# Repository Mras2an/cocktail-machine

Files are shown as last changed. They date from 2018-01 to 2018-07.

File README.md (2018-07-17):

# cocktail-machine

The goal is to be able to:
- Order a cocktail via a phone or PC
- Order a cocktail via a voice assistant (Google home, Alexa, ...).
- Order a cocktail via a IFTTT trigger

You have full documentation into the doc repertory.

## DEMO :

<a href="https://www.youtube.com/watch?v=Tx3ExhTUp6A" target="_blank">WebcamIP</a>

## CALL FOR VOLUNTEERS

After this first version I'm looking for people to help me on this open source project. The goal is to propose "pull requests" for new features or modifications.

Here is the list of features to improve the project (Do not hesitate to propose others):

| State | Addons
|---|---
| todo | Submit an UX (User eXperience) and a design for the web page
|  todo | Re-make the web page (css / html) according to the UX / design
| todo | Handling several languages on the web page
| todo | Fix the smartconfig bug
| todo | Fix potential bug
| todo | Add auto tests
| todo | Delete wifi ssid / mdp with push button
| todo | Re-make the socket part for IFTTT
| todo | Reset the A4988 module when the step motors are not used
| todo | Use the PWM for LED handling
| todo | Create doxygen documentation
| todo | And more ...

I know that any job deserves a salary but I have nothing to you offer. But I can send you a bare PCB  to make your own machine (only for the first 5 most motivated volunteers).

Please, if you are interested here is the mailing list to discuss new features or modifications: "connectedcocktailmachine@gmail.com"

Thank you for your time.

## LICENSE TERMS 

Copyright (c) 2018. Redistribution and use in source and binary forms, with or without
modification, are permitted provided that the following conditions are met:

* please cite the project [Mras2an] http://mras2an.webnode.fr/

THIS SOFTWARE IS PROVIDED BY THE REGENTS AND CONTRIBUTORS 'AS IS' AND ANY
EXPRESS OR IMPLIED WARRANTIES, INCLUDING, GO TO NOT LIMITED TO, THE IMPLIED
WARRANTIES OF MERCHANTABILITY AND FITNESS FOR A PARTICULAR PURPOSE ARE
DISCLAIMED.

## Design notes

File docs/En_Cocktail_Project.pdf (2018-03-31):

## Realization of a connected cocktail machine with an espressif WROOM32

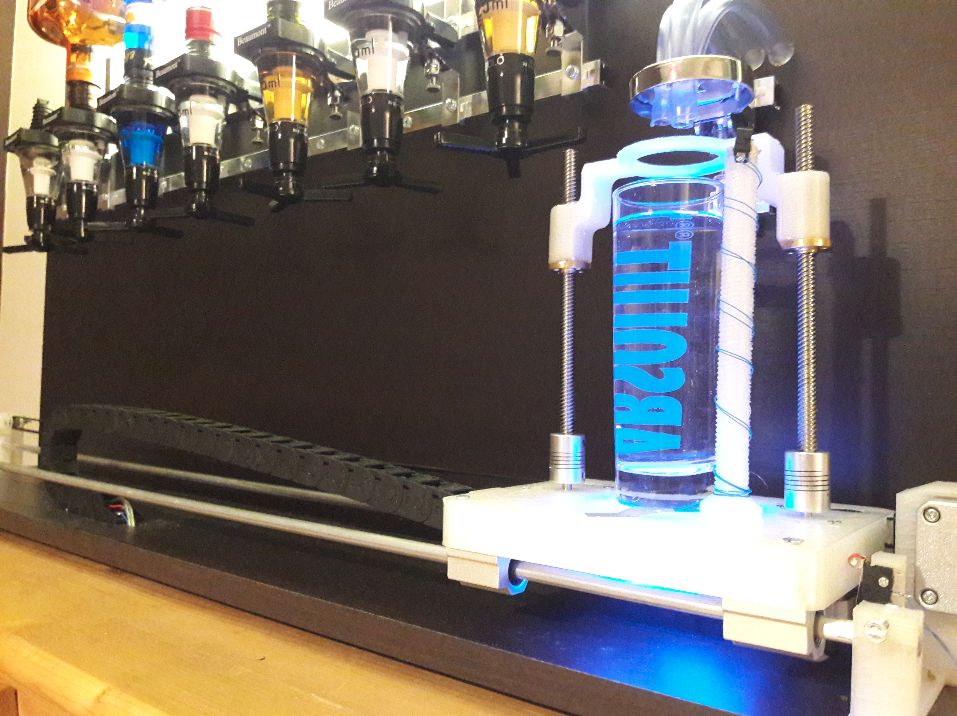
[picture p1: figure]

Revision | Data | Author | Modifications
R01 | 17/01/2018 | Q.THEROND | Creation

1) Introduction | 3
2) Sagittal diagramme | 4
2.1) Description of the links | 4
3) Functional diagram | 5
3.1) FS1.0: Power supply | 5
3.2) FS1.1: Stepper motors | 5
3.3) FS1.2: RGB LED | 6
3.4) FS1.3: uC wifi | 6
3.5) FS1.4: Sensors | 6
3.6) FS1.5: Pumps | 6
3.7) FS1.6: Expansion connectors | 7
4) Structural diagram | 8
4.1) FS1.0: Power | 9
4.1.1) Calculation of a radiator | 10
4.2) FS1.1: Step motors | 11
4.3) FS1.2: RGB LED | 12
4.4) FS1.3 : uC wifi | 13
4.4.1) Definition of the inputs, outputs of the microcontroller. | 13
4.4.1.1) Inputs | 13
4.4.1.2) Outputs | 14
4.4.1.3) Other: | 14
4.5) FS1.4: Sensors | 15
4.6) FS1.5: Pumps | 16
4.7) FS1.6: Expansion connectors | 17
5) The PCB and List of components | 18
5.1) PCB | 18
5.2) PCB List of components | 19
5.3) Meca and other: | 20
6) The software | 22
6.0) Presentation of Wifi/Bluetooth WROOM-32 module and SDK-IDF | 22
6.0.1) WROOM-32 module | 22
6.0.2) SDK-IDF | 22
6.1) Flash partition | 22
6.2) The architecture | 24
6.2.1) The espressif SDK | 24
6.2.2) The drivers | 24
6.2.3) The HAL and OSAL | 24
6.2.4) The application | 24
6.3) The features of the software | 25

6.3.1) Wi-Fi connected mode | 25
6.3.2) smartconfig mode | 26
6.3.3) Update (OTA) | 27
6.3.4) Push button | 27
6.3.5) File system | 28
6.3.6) End-of-run detection | 29
6.3.7) Web page for the cmd cocktails | 29
6.3.8) Motor control | 31
6.3.9) Step motor control | 31
6.3.10) RGB LED | 32
6.3.11) cJson | 32
6.3.12) mDNS hostname | 33
6.3.13) Voice assistant (Alexa, Google Home, ...) | 33
6.3.13.1) Configure NAT and dynDNS | 33
6.3.13.2) Create an Applet on IFTTT | 33
6.3.13.3) Open a TCP socket on the ESP32 | 34
6.3.14) Logs | 35
6.3.15) Add-on | 35
6.4) The JSON | 36
6.4.1) The JSON of the location of the bottles | 36
6.4.2) The JSON of the cocktail ingredient list. | 36
6.5) The web page | 37
6.5.1) The CSS | 37
6.5.1) HTML | 38
7) Mechanics | 40
7.1) The wood | 40
7.2) The tray | 40
8) Getting started and functioning | 41
8.1) Hardware connection | 41
8.2) Configure the software | 41
8.3) Compile and program the code | 42
8.4) First boot | 42
8.4) Movies | 44
8.5) Hygiene of the cocktail machine | 44
9) The future of the project | 45
9.1) Modify | 45
9.2) Add | 45
10) Pictures | 46

# 1) Introduction

Failing to achieve an interesting feature for the espressif SDK like wi-fi mesh I will present a fun project. The realization hardware and software of a connected cocktail machine with an espressif WROOM32. The goal is to be able to:
- Order a cocktail via a phone or PC
- Order a cocktail via a voice assistant (Google home, Alexa, ...).
- Order a cocktail via a IFTTT trigger

For that we will see different IOT functionality proposed by the WROOM32 like:
- Connect the system to internet with smartconfig
- Create a web page
- Use a mDNS and a fixed IP.
- Use a socket for IFTTT
- Update the system with OTA and the flash partition of ESP32
- Use the hardware features on the ESP (gpio, file system, ...)
- Use the FreeRTOS operating system of the espressif SDK-IDF
- Use the cJson library

And sorry for my English!

# 2) Sagittal diagramme

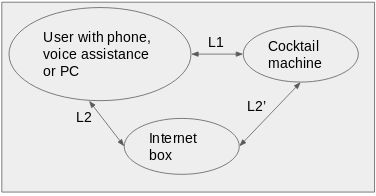
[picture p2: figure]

## 2.1) Description of the links

L2 / L2 ':
- Allows the user to order a cocktail via a web page.
- Allows the user to order a cocktail via a voice assistance (Alexa, Google Home, ...)
- Send his SSID and password with his smartphone to connect the system to the internet.
- Allows the system update with OTA
L1:
- Allows the user to put and retrieve his glass.
- Lighting information about the state of the system.
- Allows fill the bottles and clean them.

# 3) Functional diagram

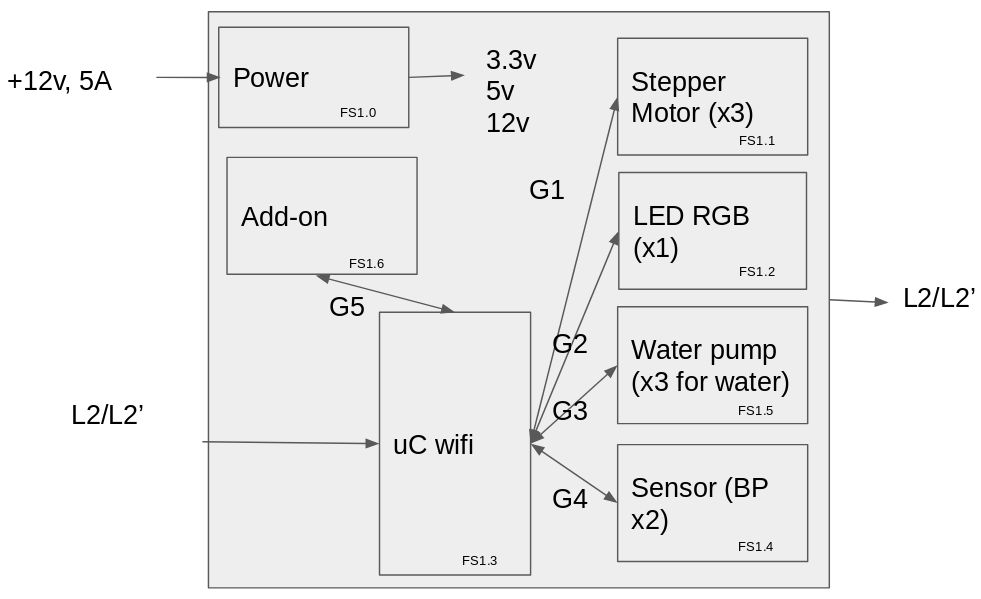
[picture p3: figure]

## 3.1) FS1.0: Power supply

The power function allows to create, thanks to an input voltage of 12V 5A, + 5V, + 3.3V, 0V.

Input(s):
12V, 5ADC.

Output(s):
+ 5V, + 3.3V, 0V

## 3.2) FS1.1: Stepper motors

The motor function allows to control the tray with the glass and to serve the cocktail via the dosers.

Input(s):
G1: Digital signals (dir and clk) for controlling the stepper motors.

Output(s):
Physical movement of the engines

## 3.3) FS1.2: RGB LED

The RGB LED informs the user of the system status.

Input(s):
G2: Digital signals to control the RGB LED.

Output(s):
L2: Lighting signals to inform the user

## 3.4) FS1.3: uC wifi

Ensures through a programmed treatment (software) the acquisition, processing and return of information. The smartconfig mode of the wroom32 allows to recover the SSID and password of the internet box. The wi-fi allows to control the system via a smartphone or a computer through a web page on a fixed IP address or with a voice assistance. It communicates with the motors, the RGB LED. sensors, and offers inputs / outputs to add additional functionality.

Input(s):
L2 / L2 ': Wifi connection in wpa2, wep, ... smartconfig mode, http web page, socket for IFTTT, OTA update
G4: Digital Signals for Limit Detection

Output(s):
L2 / L2 ': Wifi connection in wpa2, wep, ... smartconfig mode, http web page, socket for IFTTT, OTA update
G1: Digital Signals for Stepper Motor Control
G2: Digital Signals for RBG LED Control
G3: Digital signals for pump control

## 3.5) FS1.4: Sensors

Allows to delete the SSID and password of the wi-fi with a push button and the end-of-run detections.

Input(s):
L1: Physical size

Output(s):
G4: Digital signals on / off

## 3.6) FS1.5: Pumps

The "pumps" function is used to control DC motors.

Input(s):
G3: Digital signals for pump control

Output(s):
Physical movement.

## 3.7) FS1.6: Expansion connectors

Allows you to add features to the e-card.

Input(s):
G5: Digital Signals

Output(s):
G5: Digital Signals

# 4) Structural diagram

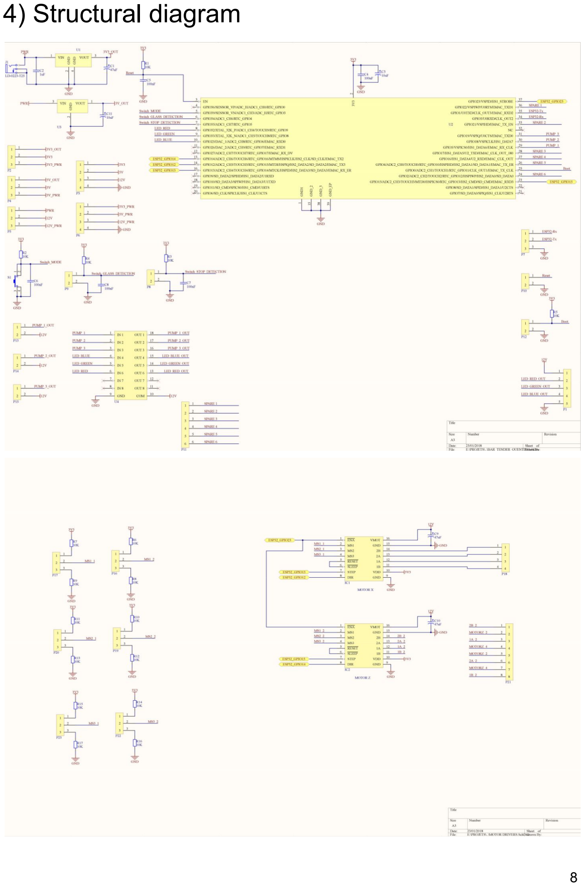
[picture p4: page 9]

## 4.1) FS1.0: Power

The power function allows to create, thanks to an input voltage of 12V 5A, + 5V and + 3.3V.

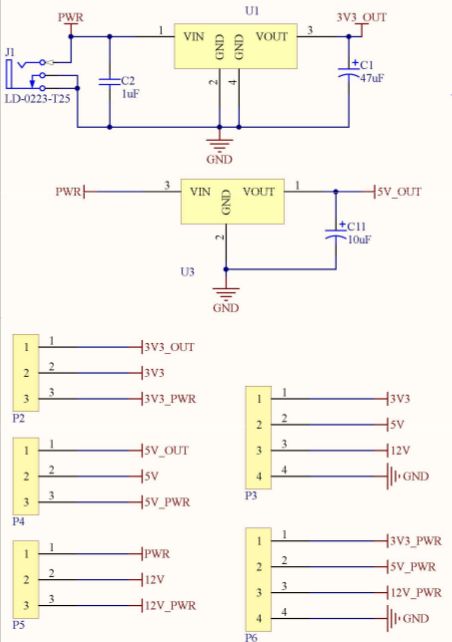
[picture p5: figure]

J1: 12v input

C1, C11: Polarized chemical capacitors. They perform the filtering, and allow a decoupling in case of power supply

C2: Plastic capacitor, serves as an anti-parasite to suppress high
frequencies (it is recommended in the technical documentation).

U3: 5V regulator, it allows to regulate the input voltage 12V DC in a voltage of 5V DC. According to the manufacturer's documentation of the 78XX, a minimum input voltage of the output voltage plus Vdrop (2V) or Ve = Vs + Vdrop = 5 + 2 = 7V minimum is required for proper operation.

U1: 3.3V LDO, it allows to regulate the input voltage 12V DC in a voltage of 3.3V DC.

P2, P4, P5: Choose the power source (internal or external) according to the current requirement. It is physically, connecting strips on which we just connect a "jumper" to select the desired voltage.

P3: Connector for testing output voltages.

P6: Connect an external power supply to not use the regulators (if more power is needed). Attention P2, P4, P5 must be connected correctly.

### 4.1.1) Calculation of a radiator

supposition: esp32=90mA, autre 50mA max
Isystem = 90+50 = 140mA
Pmax = (Tj – Ta)/RTHja = (125-25)/65 = 1,5W
Putil(3.3V) = Isystéme*(Ve-Vs) = 140*10^-3*(12-3.3) = 1,218W
Putil(5V) = Useless
Putil<Pmax.

The utility of a radiator for regulators is not essential at room temperature.

## 4.2) FS1.1: Step motors

The motor function allows to control the tray with the glass and to serve the cocktail via the dosers.

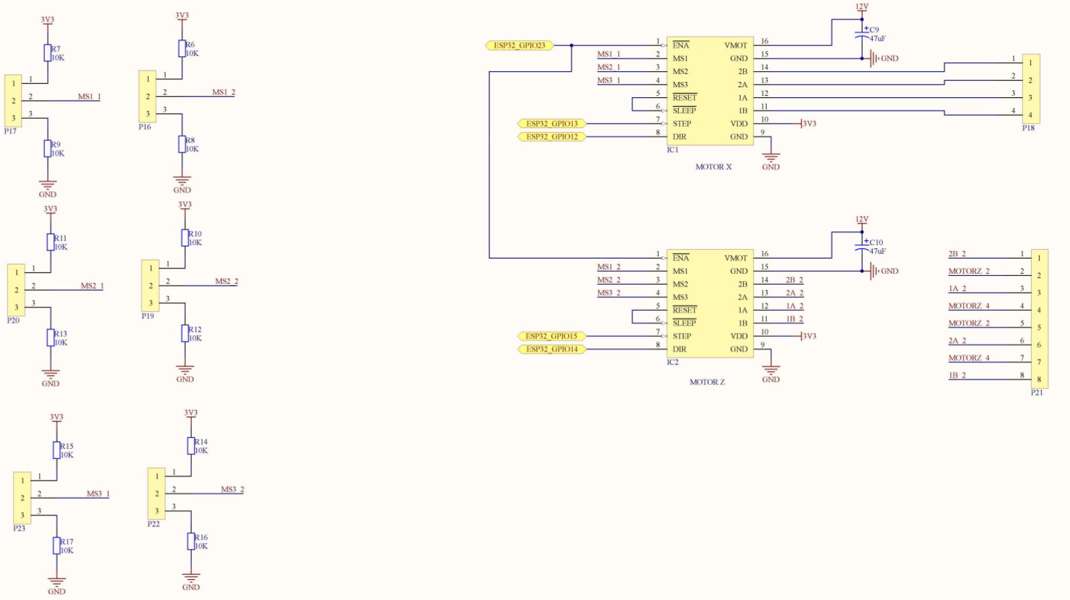
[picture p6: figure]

IC1, IC2: are modules based on A4988 for the control of stepper motors powered by 3.3v. MSI_x inputs are used to configure the step resolution. the STEP input is a clock that triggers one step per clock period. the input DIR makes it possible to choose the direction of rotation of the motor.

P16, P17, P19, P20, P22, P32: Allows you to select one of the five state resolutions according to the truth table above. For the project I am in full step.

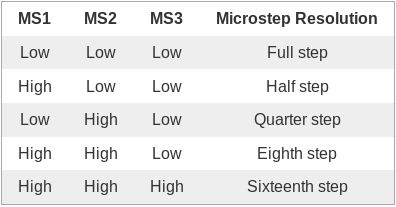
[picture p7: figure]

C9, C10: Polarized chemical decoupling capacitors.

P18: Used to connect the motor of the tray with the glass (X axis).

P21: Used to connect the motors to serve the cocktail via the dosers (Y axis).

## 4.3) FS1.2: RGB LED

The RGB LED informs the user of the system status.

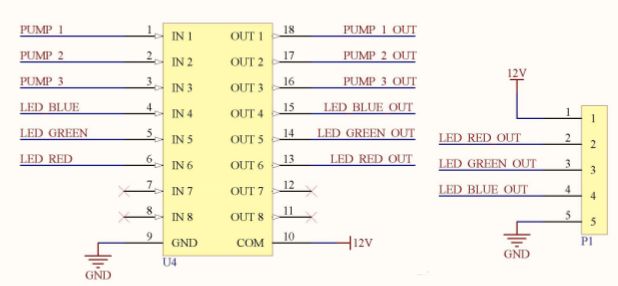
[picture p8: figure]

U4: Controlled switches (transistor network - ULN2803). Each of these 8 channels can be open or closed. It is capable of driving a load up to 500mA.

P1: Connect the RGB LED. PIN 5 is not used. You have to connect the LED as follow

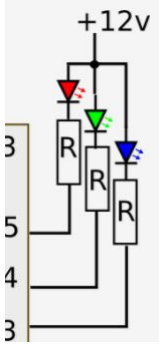
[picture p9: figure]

(source: forum.arduino.cc/index.php?topic=465854.0)

## 4.4) FS1.3 : uC wifi

Ensures thanks to a programmed treatment (software) the acquisition the treatment and the return of the information. The smartconfig mode of WROOM32 allows to recover the SSID and password of the internet box. The wifi allows to control the system via a smartphone or a computer through a web page on a fixed IP address or with a voice assistance. It communicates with the motors, the RGB LED. sensors, and offers inputs / outputs to add additional functionality.

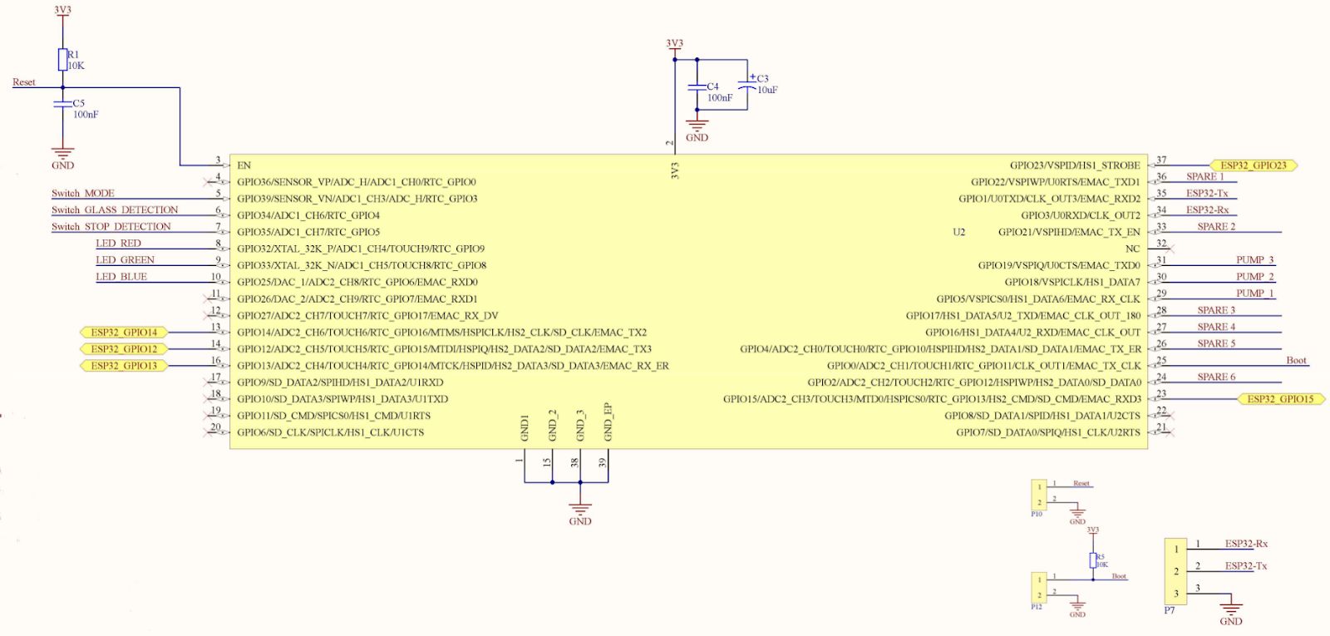
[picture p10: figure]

R1, C5, P10: Allows a reset on the wroom32.

C4, C3: used to filter high and low frequencies.

P7: Allows programming the wroom32 via a UART.

P12: Set wroom32 to programming mode.

4.4.1) Definition of the inputs, outputs of the microcontroller.
4.4.1.1) Inputs
Switch_MODE: Allows you to delete the Wi-Fi configuration (SSID and password)

Switch_GLASS_DETECTION: Detects the end of the board.

Switch_STOP_DETECTION: Used to detect the end of the dispenser management system.

Boot: Set the WROOM32 to programming mode.

Reset: Allows a reset on the WROOM32.

ESP32-Rx: Allows to send the binaries to be saved in memory of the wroom32

4.4.1.2) Outputs
ESP32_GPIO14, 12, 13, 15: Used to control the direction of rotation of motors and the speed of steps.

ESP32_GPIO23: Allows you to enable and disable A4988-based modules

LED_RED: Used to control the red LED. When the system starts, the LED is red as long as the system has not reached the limit

LED_GREEN: Used to control the green LED. Not used yet.

LED_BLEU: Used to control the BLUE LED. The blue fix indicates that the system is ready for use. The blinking blue indicates that the system is in preparation for a cocktail party.

ESP32-Tx: Allows you to send information to the programming tool.

PUMP_1 to PUMP_3: Used to control pumps.

4.4.1.3) Other:
SPARE1 to SPARE6: The SPARE inputs / outputs allow you to add new features to the cocktail machine such as milk powder dosing (of course, this implies a whole system of milk preservation and hygiene. given as an example.)

## 4.5) FS1.4: Sensors

Allows to delete the SSID and password of the wi-fi with a push button and the end-of-run detections.

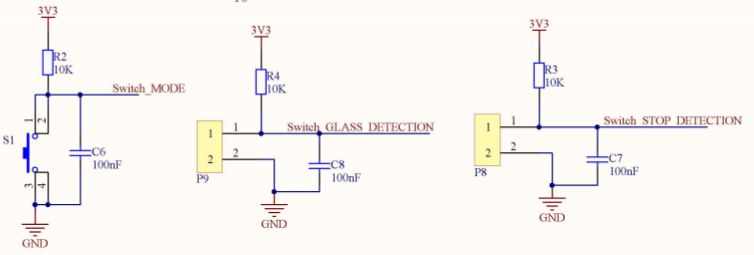
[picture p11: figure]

R2, R3, R4: Pull-up resistance.

C6, C7, C8: Anti-rebound capacitor.

P9, P8: Used to connect the limit switches.

## 4.6) FS1.5: Pumps

The pump function is used to control DC motors.

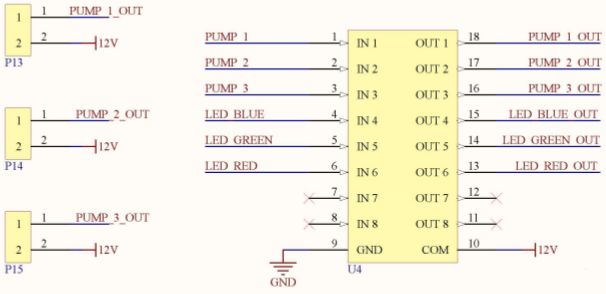
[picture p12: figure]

P13, P14, P15: Used to connect the pumps.

U4: Switches controlled. Each of these 8 channels can be open or closed. It is capable of driving a load up to 500mA. After the tests the chosen pump consumes more than 500mA, so I added an expansion board with relays. You can connect your relays on P13, P14, P15 as follow.

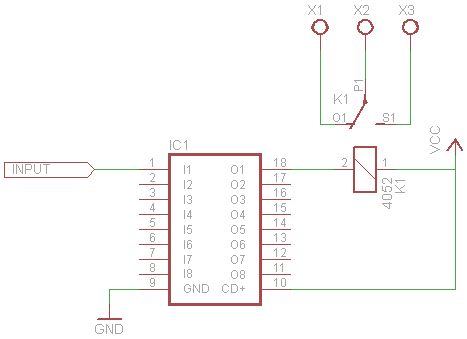
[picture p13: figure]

(source: www.brunwinkel.de/elektronik/ics/uln2803/)

## 4.7) FS1.6: Expansion connectors

Allows you to add features to the board.

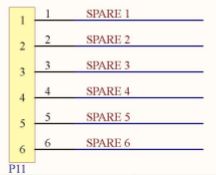
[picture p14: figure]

P11: Used to connect another electronic board to the central unit.

# 5) The PCB and List of components

## 5.1) PCB

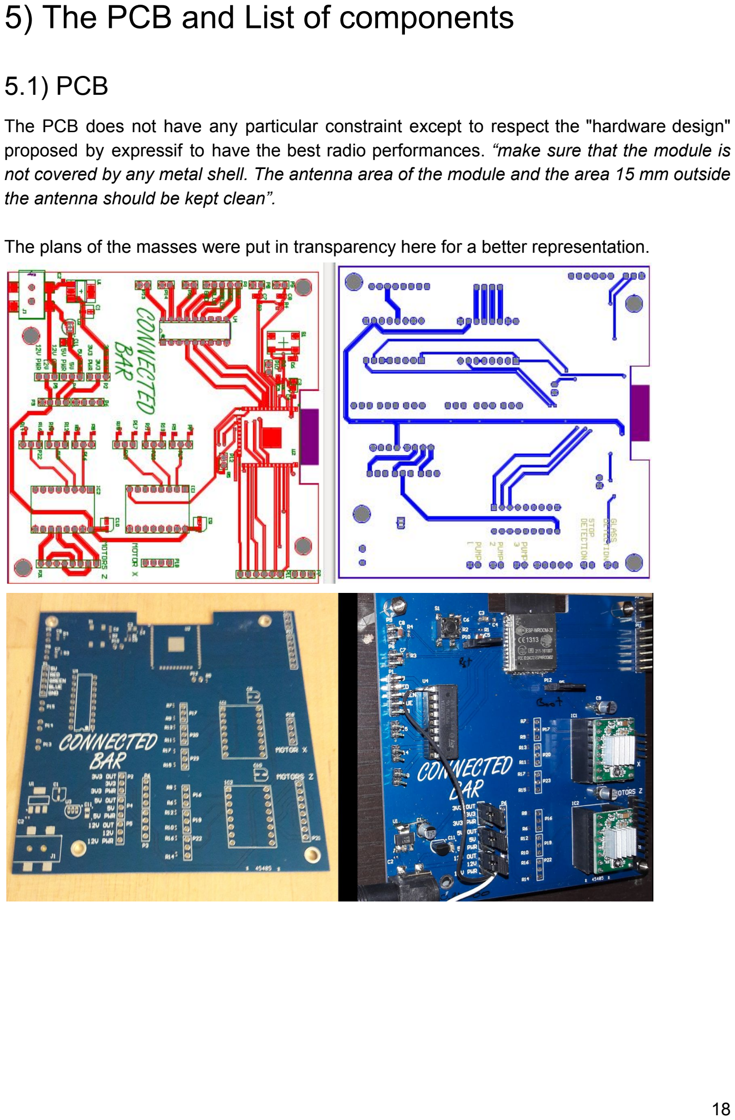
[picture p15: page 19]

The PCB does not have any particular constraint except to respect the "hardware design" proposed by expressif to have the best radio performances. “make sure that the module is not covered by any metal shell. The antenna area of the module and the area 15 mm outside the antenna should be kept clean”.

The plans of the masses were put in transparency here for a better representation.

# 5.2) PCB List of components

Comment | Description | Designator | Footprint | LibRef | Quantity
EEEFK0J470UR | CAP 47uF 6.3V ALU CMS | C1, C9, C10 | CAPA CHIMIQUE CMS | EEEFK0J470UR | 3
GRM155R60J105KE1 9D | CAP 1UF 6V3 X5R CER 0402 CMS | C2 | 0402 | GRM155R60J105KE1 9D | 1
0805YD106KAT2A | CAP 10uF 16V X5R CER 0805 CMS | C3, C11 | 0805 POLARISE | 0805YD106KAT2A | 2
CC0402KRX7R6BB10 4 | CAP 100NF K10V X7R CER 0402 CMS | C4 | 0402 | CC0402KRX7R6BB10 4 | 1
MC0603B104K250CT | CAP 100NF 25V X7R CER 0603 CMS | C5, C6, C7, C8 | 0603 | MC0603B104K250CT | 4
A4988 | MOTOR DRIVER | IC1, IC2 | DRIVER MOTEUR | A4988 | 2
LD-0223-T25 | CMS JACK SOCKET PLUG | J1 | PJACK-LIHSHE NG-LD-0223-25 | LD-0223-T25 | 1
HEADER 1x5 | EMBASE MALE 1 RANGEE VERT 5 VOIES | P1 | EMBASE 5 VOIES | HEADER 1x5 | 1
HEADER 1x3 | EMBASE MALE 1 RANGEE VERT 3VOIES | P2, P4, P5, P7, P16, P17, P19, P20, P22, P23 | EMBASE 3 VOIES | HEADER 1x3 | 10
HEADER 1x4 | EMBASE MALE 1 RANGEE VERT 4 VOIES | P3, P6, P18 | EMBASE 4 VOIES | HEADER 1x4 | 3
HEADER 1x2 | EMBASE MALE 1 RANGEE VERT 2 VOIES 2.54mm | P8, P9, P10, P12, P13, P14, P15 | EMBASE 2 VOIES - 2.54mm | HEADER 1x2 - 2.54 mm | 7
HEADER 1x6 | EMBASE MALE 1 RANGEE VERT 6 VOIES | P11 | EMBASE 6 VOIES -VERTICAL | HEADER 1x6 | 1
HEADER 1x8 | EMBASE MALE 1 RANGEE VERT 8 VOIES | P21 | EMBASE 8 VOIES -VERTICAL | HEADER 1x8 | 1

MC 0.0625W 0402 1% 10K | RESIST.CMS 0402 1/16W 5% 10K | R1, R2, R3, R4, R5, R6, R7, R8, R9, R10, R11, R12, R13, R14, R15, R16, R17 | 0402 | MC 0.0625W 0402 1% 10K | 17
Switch | SWITCH TACTILE | S1 | TACT SWITCH 6X6 | DTSM-61R-V-* | 1
LM3940IMP-3.3/NOP B | REGULATEUR LINEAIRE 3V3 | U1 | SOT-223 | LM3940IMP-3.3/NOP B | 1
ESP-WROOM-32 | MODULE WIFI ESPRESSIF WROOM 32 | U2 | MODULE_WIFI ESPRESSIF WROOM 32 | ESP WROOM 32 | 1
LM78L05ACZ/NOPB | REGULATEUR LINEAIRE 5V | U3 | TO-92 | LM78L05ACZ/NOPB | 1
ULN2803A | Transistor en réseau bipolaire | U4 | DIP 18 | ULN2803A | 1

## 5.3) Meca and other:

BQLZR 500mm Longueur 8mm Diam¨¨tre ext¨¦rieur Axe linéaire horizontal Axe optique Ensemble de palier ¨¤ glissi¨¨re et axe linéaire Ensemble de soutien https://www.amazon.fr/gp/product/B01K4MX1WW/ref=oh_aui_detailpage_o03_s00?ie=UTF8&psc=1 (https://www.amazon.fr/gp/product/B01K4MX1WW/ref=oh_aui_detailpage_o03_s00?ie=UTF8&psc=1)

Myarmor 2 pcs 2 GT 20 dents Timing Poulie de roue + 5 m 2 Gt-6 mm Ouverture en caoutchouc Ceinture

https://www.amazon.fr/gp/product/B01K4MX1WW/ref=oh_aui_detailpage_o03_s00?ie=UTF8&psc=1 (https://www.amazon.fr/gp/product/B01K4MX1WW/ref=oh_aui_detailpage_o03_s00?ie=UTF8&psc=1)

XCSOURCE NEMA 17 2 Phase Moteur 4-Wire 1.8A Stepper 42 * 42 * 34mm Pour Imprimante 3D TE225 | https://www.amazon.fr/gp/product/B011NRMXYO/ref=oh_aui_detailpage_o02_s00?ie=UTF8&psc=1 (https://www.amazon.fr/gp/product/B011NRMXYO/ref=oh_aui_detailpage_o02_s00?ie=UTF8&psc=1)
Chenxi Shop 15 x 15 mm L1000 mm Plastique câble Drag Fil de chaîne de transport pour CNC Router machine | https://www.amazon.fr/gp/product/B073XFG975/ref=oh_aui_detailpage_o03_s00?ie=UTF8&psc=1 (https://www.amazon.fr/gp/product/B073XFG975/ref=oh_aui_detailpage_o03_s00?ie=UTF8&psc=1)
Doseur d'alcool Beaumont 25ml | https://www.amazon.fr/gp/product/B009VJ4M32/ref=oh_aui_detailpage_o04_s00?ie=UTF8&psc=1 (https://www.amazon.fr/gp/product/B009VJ4M32/ref=oh_aui_detailpage_o04_s00?ie=UTF8&psc=1)
SODIAL(R) 10 Pcs Mini Micro Fin de course Levier a galet bras SPDT Declic LOT | https://www.amazon.fr/gp/product/B00U8MPR8U/ref=oh_aui_detailpage_o07_s00?ie=UTF8&psc=1 (https://www.amazon.fr/gp/product/B00U8MPR8U/ref=oh_aui_detailpage_o07_s00?ie=UTF8&psc=1)

Transformateur 220Vac vers 12Vdc Chargeur Alimentation à découpage pour guirlande Ruban Led Bande 5m 60W | https://www.amazon.fr/gp/product/B06WGRXCPK/ref=oh_aui_detailpage_o05_s00?ie=UTF8&psc=1 (https://www.amazon.fr/gp/product/B06WGRXCPK/ref=oh_aui_detailpage_o05_s00?ie=UTF8&psc=1)
TecTake Boissons cuillère pour 6 bouteilles pour le mur bouteille support bar butler | https://www.amazon.fr/gp/product/B0196P9XR0/ref=oh_aui_detailpage_o07_s00?ie=UTF8&psc=1 (https://www.amazon.fr/gp/product/B0196P9XR0/ref=oh_aui_detailpage_o07_s00?ie=UTF8&psc=1)
Anycubic 20 Dents Alumium Timing Poulie 5mm Alésage Ceinture Roue D’entraînement pour 10mm Largeur GT2 Ceinture 5PCS | https://www.amazon.fr/gp/product/B06XT274LH/ref=oh_aui_detailpage_o08_s00?ie=UTF8&psc=1 (https://www.amazon.fr/gp/product/B06XT274LH/ref=oh_aui_detailpage_o08_s00?ie=UTF8&psc=1)
Popprint 5 pcs Ramps1.4 A4988 pilote de moteur pas à pas avec dissipateur thermique pour imprimante 3d, Green, 5 | https://www.amazon.fr/gp/product/B06Y28H956/ref=oh_aui_detailpage_o00_s00?ie=UTF8&psc=1 (https://www.amazon.fr/gp/product/B06Y28H956/ref=oh_aui_detailpage_o00_s00?ie=UTF8&psc=1)
Anself Ultra silencieux Micro Mini DC12V Pompe à eau | https://www.amazon.fr/gp/product/B00OIHLTME/ref=oh_aui_detailpage_o03_s01?ie=UTF8&psc=1 (https://www.amazon.fr/gp/product/B00OIHLTME/ref=oh_aui_detailpage_o03_s01?ie=UTF8&psc=1)

# 6) The software

It is available with this document in zip file and on github https://github.com/Mras2an/cocktail-machine

## 6.0) Presentation of Wifi/Bluetooth WROOM-32 module and SDK-IDF

### 6.0.1) WROOM-32 module

I chose the Wi-fi/Bleutooth WROOM-32 module because this module has many advantages. Like an attractive price (for a wi-fi module), a nice memory capacity, a simple and complete SDK with lot of example and a stable wi-fi connection. So it's a great choice for making a homemade connected cocktail machine. But like all products, it also has drawbacks. The disadvantages of the resident module is in the flash protection management which requires 30 seconds (at first boot) to encrypt the 4Mb. It also lacks real hardware acceleration for ssl handshake (between 1 and 5 seconds for RSA256 in 2048).

### 6.0.2) SDK-IDF

I chose SDK-IDF on 2.1 branch instead of Arduino SDK because I already know the Arduino SDK. The SDK-IDF has a lot of contributors and I was able to propose three patches for the SDK-IDF. My pull requests was integrated in cind days, so the project maintainers are responsive.

## 6.1) Flash partition

To allow the update of the system via the wifi we need more partition. Espressif proposes the possibility of creating a cvs file to define the addresses. Here is the one of the cocktail machine:
# Name, Type, SubType, Offset, Size, Flags

otadata,data,ota,0xd000,8K,
phy_init,data,phy,0xf000,4K, factory,app,factory,0x10000,1M, ota_0,app,ota_0,0x110000,1M, ota_1,app,ota_1,0x210000,1M, nvs,data,nvs,0x315000,500K,

So we have a partitioned memory as follows:
| Addr | Binaries
| 0x001000 | Bootloader.bin
| 0x008000 | Partitions.bin
| 0x010000 | Factory.bin
| 0x110000 | OTA_0.bin
| 0x210000 | OTA_1.bin
| 0x315000 | NVS (500Ko)
| 0x3F0000 | Free

## 6.2) The architecture

The software is architectured as follows:

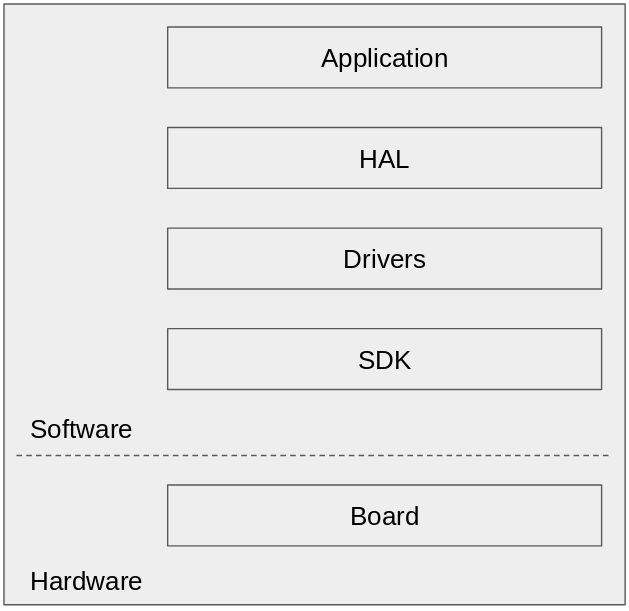
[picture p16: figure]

### 6.2.1) The espressif SDK

The SDK used is the SDK-IDF on the v2.1 branch available on github at (https://github.com/espressif/esp-idf). This is the official development system of the ESP32 chip.

### 6.2.2) The drivers

Used for different hardware interactions such as motors, the RGB LED, or the functionality of the WROOM32 module (Gpio, wifi, smartconfig, OTA, ...).

### 6.2.3) The HAL and OSAL

HAL ans OSAL allows simple porting of cocktail machines to another SDK, OS, or hardware platform.

### 6.2.4) The application

The application proposes the web page and the management of cocktails, the OTA update and a socket to read IFTTT command.

## 6.3) The features of the software

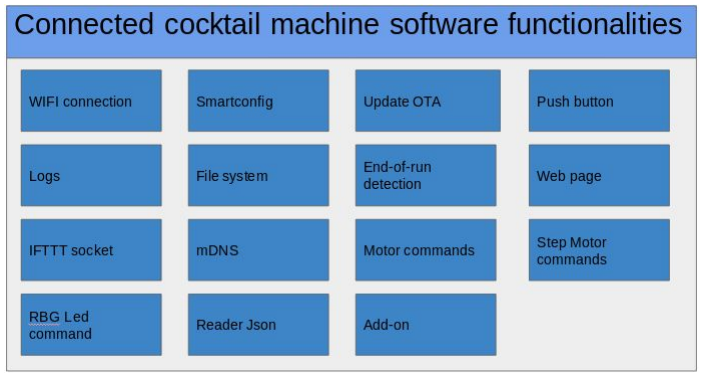
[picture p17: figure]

### 6.3.1) Wi-Fi connected mode

Connection to an internet box with WEP, WPA-PSK [TKIP], WPA2-PSK [AES] or WPA-PSK [TKIP] + WPA2-PSK [AES] security.
The function Esp32wifi_init allows you to set the wi-fi for your country and fill the structure "wifi_config_t" with your SSID and password.
wifi_init_config_t cfg = WIFI_INIT_CONFIG_DEFAULT(); ESP_ERROR_CHECK(esp_wifi_init(&cfg)); ESP_ERROR_CHECK(esp_wifi_set_storage(WIFI_STORAGE_RAM)); ESP_ERROR_CHECK(esp_wifi_set_mode(WIFI_MODE_STA)); wifi_config_t sta_config = Esp32Wifi_getSSIDAndPass(); ESP_ERROR_CHECK(esp_wifi_set_config(WIFI_IF_STA, &sta_config)); ESP_ERROR_CHECK(esp_wifi_set_country(WIFI_COUNTRY_EU)); ESP_ERROR_CHECK(esp_wifi_start());

The Esp32_init function is used to configure an ip static on the wroom32. If your network is not 192.168.1.x with a mask in 255.255.255.0 you must modify the code below. tcpip_adapter_init();
ESP_ERROR_CHECK(tcpip_adapter_dhcpc_stop(TCPIP_ADAPTER_IF_STA)); tcpip_adapter_ip_info_t info = { 0,};
IP4_ADDR(&info.ip, 192, 168, 1, 51);
IP4_ADDR(&info.gw, 192, 168, 1, 1);
IP4_ADDR(&info.netmask, 255, 255, 255, 0); ESP_ERROR_CHECK(tcpip_adapter_set_ip_info(TCPIP_ADAPTER_IF_STA, &info))

### 6.3.2) smartconfig mode

Allows sending the SSID and password in wi-fi broadcast. When the system has finished smartconfig the task Esp32SmartConfig_task saves the information in memory. if((this->pass != NULL) && (this->ssid != NULL))
{
Wifi_saveSSIDAndPass(this->ssid, this->pass);
OsFree(this->ssid);
OsFree(this->pass);
}
If the backup file exists then the smartconfig task is not enable to boot. void Esp32SmartConfig_init(void)
{
this->smartConfigEnable = 0;
char * ssid = (char *)Wifi_getSsid();
char * pass = (char *)Wifi_getPassword();

if((ssid == NULL) || (pass == NULL))
{
this->smartConfigEnable = 1; wifi_event_group = xEventGroupCreate(); this->ssid = NULL;
this->pass = NULL;
}

if(ssid != NULL)
OsFree(ssid);

if(pass != NULL)
OsFree(pass);
}

void Esp32SmartConfig_createTask()
{
if(this->smartConfigEnable)
OsTaskCreate(Esp32SmartConfig_task, "Esp32SmartConfig_task", 4096, NULL, 3, NULL);
}
You can see Esp32SmartConfig.c for more informations.

I choose the smatconfig mode instead of blufi (bluetooth wifi config connection to ap) because there is no example of smartphone application for Ios. While there are Andoid and Ios example apps for smartconfig mode.

### 6.3.3) Update (OTA)

Allows updating via wifi. To start the OTA functionality I used the cocktail machine web page. When you click on the Update button, the system reboot and start the update task.
char * update = Fs_read("Update", "Update"); if (update != NULL)
{
BarDebug_info("LED GREEN\n"); LedRGBHandling_ExecuteLedTaskFromISR(GREEN_LED); Fs_delete("Update", "Update");
OsFree(update);
Ota_InitTask();
}
I have integrate the example of "classycodeoss" for the update function. We need of 3 functions, Esp32Ota_begin, Esp32Ota_writeHexData, and Esp32Ota_end. This functions
use | espressif | SDK | OTA | functions: | esp_ota_begin, | esp_ota_write,
esp_ota_get_boot_partition, esp_ota_end. When the connected cocktail machine boot you can see in the log the current partition (Factory, OTA_0, OTA_1). this address partition is laid out in the customPart file seen above.
void Esp32Ota_init()
{
const esp_partition_t * currentBootPartition = esp_ota_get_boot_partition(); memset(this->currentPartition, '\0', PART_LEN); memcpy(this->currentPartition, currentBootPartition->label, strlen(currentBootPartition->label));
this->addr = currentBootPartition->address;
BarDebug_info("Part: %s, addr:%08x \n", Esp32Ota_getCurrentPartition(), Esp32Ota_getCurrentBootAddr());
}

### 6.3.4) Push button

Allows you to delete the SSID and wifi password. The button is managed by an OS task (Idel, rising edge and falling edge).
typedef enum eButtonMode_t
{
IDLE_BUTTON,
RISING_BUTTON,
FALLING_BUTTON
} eButtonMode_t;

### 6.3.5) File system

It is an abstraction of the NVS espressif SDK functions
#define Fs_write Esp32Fs_write

esp_err_t Esp32Fs_write(const char * filename, const char * data, const char * key) {
nvs_handle my_handle;
esp_err_t err;
err = nvs_open(filename, NVS_READWRITE, &my_handle);

if(err != ESP_OK)
{
BarDebug_err("Open: %x\n", err);
return err;
}

err = nvs_set_str(my_handle, key, data);

if(err != ESP_OK && err != ESP_ERR_NVS_NOT_FOUND) {
BarDebug_err("Write: %x\n", err); nvs_close(my_handle);
return err;
}

err = nvs_commit(my_handle);

if(err != ESP_OK)
{
BarDebug_err("Commit: %x\n", err); nvs_close(my_handle);
return err;
}

nvs_close(my_handle);
return err;
}
Lets you read or write data to a file system. Example for the SSID and password wi-fi. if(Fs_write(SSID_WIFI_FILE, ssid, SSID_WIFI_FILE) != ESP_OK)
{
BarDebug_err("Error to save SSID\n");
}

if(Fs_write(PASSWORD_WIFI_FILE, password, PASSWORD_WIFI_FILE) != ESP_OK) {
BarDebug_err("Error to save password\n");
}

### 6.3.6) End-of-run detection

Allows you to initialize the system using the "MotorHandling_setInitialPosition" function. This function is called at startup and at each cocktail request.
uint32_t bp1[1], bp2[1];
BarDebug_info("Set motor at the initial position on y...\n");
Gpio_get(DETECTION_AXE_Y, bp2); BAR_ERROR_CHECK(Gpio_set(MOTOR_AXE_Y_DIR, BAR_LEVEL_HIGH)); int end = MOTOR_LIMIT;
while(bp2[0] && (end != 0))
{
Gpio_get(DETECTION_AXE_Y, bp2); BAR_ERROR_CHECK(Gpio_set(MOTOR_AXE_Y_CLK, BAR_LEVEL_LOW)); CpuDelay_ms(1);
BAR_ERROR_CHECK(Gpio_set(MOTOR_AXE_Y_CLK, BAR_LEVEL_HIGH)); CpuDelay_ms(1);
end--;
}
BarDebug_info("Motor is now at the initial position on y.\n");
BarDebug_info("Set motor at the initial position on x...\n"); Gpio_get(DETECTION_AXE_X, bp1); BAR_ERROR_CHECK(Gpio_set(MOTOR_AXE_X_DIR, BAR_LEVEL_HIGH)); while(bp1[0])
{
Gpio_get(DETECTION_AXE_X, bp1); BAR_ERROR_CHECK(Gpio_set(MOTOR_AXE_X_CLK, BAR_LEVEL_LOW)); CpuDelay_ms(1);
BAR_ERROR_CHECK(Gpio_set(MOTOR_AXE_X_CLK, BAR_LEVEL_HIGH)); CpuDelay_ms(1);
}

BarDebug_info("Motor is now at the initial position on x.\n");

### 6.3.7) Web page for the cmd cocktails

Allows you to order a cocktail. Once the system connected to the wi-fi network is called "Cocktail_init" and "QueueCocktail_init".
The "Cocktail" task will retrieve the JSON information to save it in RAM in the structures below:
typedef struct
{
char name[MAX_NAME_SIZE];
char note[MAX_NOTE_SIZE_FOR_BOTTLE]; int position;
} sBottle;

typedef struct

{
char name[MAX_NAME_SIZE];
int measure;
} sIngredient;

typedef struct cocktail
{
char name[MAX_NAME_SIZE];
sIngredient ingredient[MAX_INGREDIENT]; } sCocktail;

sCocktail cocktail[MAX_COCKTAIL];
sBottle bottle[MAX_BOTTLE];

When the "Cocktail" task has finished retrieving the information we call "Html_init". Who will create the HTML web page.
html_indexBegin(http_index_hml);
html_indexTitle(http_index_hml);
html_tabBegin(http_index_hml); html_tabColumnBegin(http_index_hml, "Selection"); html_tabColumnMiddle(http_index_hml, "Ajouter"); html_tabColumnEnd(http_index_hml, "Fourni"); Cocktail_createHtmlCodeForCocktails(http_index_hml);
html_tabEnd(http_index_hml);
html_indexEnd(http_index_hml);

The function "Cocktail_createHtmlCodeForCocktails" will sort the available ingredients according to the bottles on the cocktail machine. This allows you to tell the user which ingredients are unavailable.
for(i = 0; i < MAX_COCKTAIL; i++)
{
for(j = 0; j < MAX_INGREDIENT; j++)
{
if(cocktail[i].ingredient[j].name[0] != '\0')
{
if(Cocktail_isBottleExiste(cocktail[i].ingredient[j].name))
{

The "QueueCocktail_receivedTask" task is called when a user selects a cocktail on the web page. If we ask for three cocktails then they will be put on the waiting list. The variable "goToPosition" and "currentPosition" make it possible to calculate the future position of the tray according to the current state.
OsQueueReceive(pCtx->xQueueCocktailEventQueue, &QueueCocktail, OsPortTimingPeriod);
LedRGBHandling_ExecuteLedTaskFromISR(BLUE_LED_FAST_BLINKING);

MotorHandling_setInitialPosition();
int nbIngredients = Cocktail_getDispoIngredients(bottleList.bottle, bottleList.position, bottleList.measure, QueueCocktail);
int goToPosition = 0;
int currentPosition = 0;
for(int i = 0; i < nbIngredients; i++)
{
if(currentPosition != bottleList.position[i])
{
goToPosition = bottleList.position[i] - currentPosition; MotorHandling_setPositionOnX(goToPosition); currentPosition += goToPosition;
CpuDelay_ms(500);
}
if(currentPosition != 0)
{
MotorHandling_getAMeasureOnY(bottleList.measure[i]); }
else
{
MotorHandling_getAMeasureOnPump(bottleList.measure[i]); }

}
MotorHandling_setInitialPosition(); LedRGBHandling_ExecuteLedTaskFromISR(BLUE_LED);

### 6.3.8) Motor control

Used to control a DC motor in position 0. For the moment only one motor is possible. BAR_ERROR_CHECK(Gpio_set(MOTOR_PUMP_1, BAR_LEVEL_HIGH)); for(int j = 0; j < measure; j++)
{
CpuDelay_ms(1000);
}
BAR_ERROR_CHECK(Gpio_set(MOTOR_PUMP_1, BAR_LEVEL_LOW));

### 6.3.9) Step motor control

Controls the X and Y axes and their senses. Below is an example for the X axis. The "MOTOR_OFFSET" allows to advance the plate of 10cm (distance between each bottle). "MOTOR_OFFSET" is calculated according to the degree of a step and the perimeter of the pulley.
if(position > 0)
{
BAR_ERROR_CHECK(Gpio_set(MOTOR_AXE_X_DIR, BAR_LEVEL_LOW)); end = position * MOTOR_OFFSET;
}
else

{
BAR_ERROR_CHECK(Gpio_set(MOTOR_AXE_X_DIR, BAR_LEVEL_HIGH)); end = (position * (-1)) * MOTOR_OFFSET;
}

for(int i = 0; i < end; i++)
{
BAR_ERROR_CHECK(Gpio_set(MOTOR_AXE_X_CLK, BAR_LEVEL_LOW)); CpuDelay_ms(1);
BAR_ERROR_CHECK(Gpio_set(MOTOR_AXE_X_CLK, BAR_LEVEL_HIGH)); CpuDelay_ms(1);
}

### 6.3.10) RGB LED

Used to control the color of the LED to inform the user. This is a task that manages the timing of the flashing. The variable "enableLed" allows to enable or disable the LED. The variable "queueReceiveDelay" is used to manage the flashing speed in milliseconds. OsQueueReceive(tsQueueForLed, &eAsyncMsg, queueReceiveDelay);
eAsyncCurrent = eAsyncMsg;

if(IDEL_LED == eAsyncMsg)
{
LedRGBGpioDriver_SetColor(LED_NOT_DEFINED);
}
else if((BLUE_LED_FAST_BLINKING | enableLed) == eAsyncMsg)
{
queueReceiveDelay = BLINK_FAST; if(!LedRGBGpioDriver_ToggleColor(LED_BLUE))
{
BarDebug_info("LED NOT DEFINED"); }
}

### 6.3.11) cJson

Allows to recover the fields of JSON thanks to the cJon library. Here is an example to retrieve information from a bottle.
cJSON * _name = cJSON_GetObjectItem(_bottle, "name");
if(_name != NULL)
{
cJSON * _note = cJSON_GetObjectItem(_bottle, "note");
if(_note != NULL)
{
cJSON * _position = cJSON_GetObjectItem(_bottle, "position"); if(_position != NULL)
{
memcpy(bottle[i].name, _name->valuestring, strlen(_name->valuestring));

memcpy(bottle[i].note, _note->valuestring, strlen(_note->valuestring)); bottle[i].position = (int) _position->valuedouble;

### 6.3.12) mDNS hostname

Allows access to the web page without the ip address. Example: http://mybar.local/ instead of http://192.168.1.51. It works on my PC but not on my phone.
mdns_server_t * mdns = NULL;
mdns_init(TCPIP_ADAPTER_IF_STA, &mdns);
ESP_ERROR_CHECK( mdns_set_hostname(mdns, "mybar") ); ESP_ERROR_CHECK( mdns_set_instance(mdns, "mybar") );
ESP_ERROR_CHECK( mdns_service_add(mdns, "_http", "_tcp", 80) ); ESP_ERROR_CHECK( mdns_service_instance_set(mdns, "_http", "_tcp", "mybar") );

You can also ping the cocktail machine with:
$ ping mybar.local
PING mybar.local (192.168.1.51) 56(84) bytes of data.
64 bytes from 192.168.1.51: icmp_seq=1 ttl=255 time=5.07 ms 64 bytes from 192.168.1.51: icmp_seq=2 ttl=255 time=2.76 ms

### 6.3.13) Voice assistant (Alexa, Google Home, ...)

To add a compatibility between the connected cocktail machine and a voice assistant we have lot of possibility. The most simple is to use IFTTT (If This Then That) to send a curl request to the ESP32 with "webhooks". For that we need to configure NAT and dynDNS on the internet box, create an Applet on IFTTT and open a TCP socket on the ESP32.

6.3.13.1) Configure NAT and dynDNS
we need to configure the NAT on our internet box to make a redirection on our public IP on our local IP. As our public IP is dynamic we use dynDNS as a DNS service to have a fixed domain name. All this configuration can be make on you internet box manager web page.

The domain name used is useful for the IFTTT trigger

6.3.13.2) Create an Applet on IFTTT
To create an applet on IFTTT with Google home, we have to create an account on "https://ifttt.com/". Click on "New applet". You will see (if "this" then "that"). Click on "this", select "Google assistant" and follow the instructions. After that click on “that”, select "Webhooks", and follow the instructions. Webhooks, allows to send a "curl request" on the cocktail machine

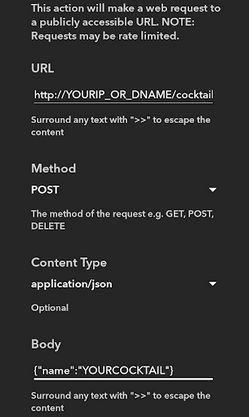
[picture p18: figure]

In my example I use "Google home", but you can make the same trigger with "Alexa", "Button widget", "location", "date & time", and more. Example with "Button widget" you can create a favorite cocktail widget on your desk phone.

6.3.13.3) Open a TCP socket on the ESP32
To open a TCP socket on the ESP32 I use "socket", "bind", "accept" functions. I use "read" and "write" functions for data communications. when I receive the "request post" send by IFTTT, I check if the cocktail name is available in the cocktail list and I answer the HTTP status code "HTTP/1.1 204" or "HTTP/1.1 400".
static const char HeadPostHttp[] = "HTTP/1.1 204 No Content\r\n\r\n";
static const char HeadPostHttpErr[] = "HTTP/1.1 400 Bad Request\r\n\r\n";
cJSON * _name = cJSON_GetObjectItem(_root, "name");
if(_name != NULL)
{
int numCocktail = Cocktail_isCocktailExiste(_name->valuestring);

if(numCocktail != 255)
{
write(sock, HeadPostHttp, strlen(HeadPostHttp)); QueueCocktail_received(numCocktail);
}
else
{
write(sock, HeadPostHttpErr, strlen(HeadPostHttpErr)); }
}

### 6.3.14) Logs

I have two logs level defined by "BAR_DEBUG", info level and error level. If "BAR_DEBUG" is defined info and error logs is enable. If "BAR_DEBUG" is not defined only error level is available.
#ifdef BAR_DEBUG

#define BarDebug_info(msg, ...) OsPrintf("[INFO: %s, L%d] "msg, __FUNCTION__, __LINE__, ##__VA_ARGS__)

#define BarDebug_err OsDebug_err

#else

#define BarDebug_info(msg, ...) #define BarDebug_err OsDebug_err #endif

### 6.3.15) Add-on

Nothing yet.

## 6.4) The JSON

there are two JSONs in the project. The first allows to define the location of the bottles and the second the list is ingredient of the cocktails.

### 6.4.1) The JSON of the location of the bottles

The "bottles" table below is a bottle list with a name and a position. Te careful the position must exist physically on the cocktail machine. Position 0 is the initial position of the tray.
{
"bottles": [{
"bottle": {
"name": "eau",
"note": "0%/vol",
"position": 0
}
}, {
"bottle": {
"name": "jus de pomme",
"note": "0%/vol",
"position": 1
}
},
….
}]
}
6.4.2) The JSON of the cocktail ingredient list.

The cocktail table below is a cocktail list. A cocktail must have a name and a table "ingredients" which is an ingredient list. Each ingredient has a name (which is not necessarily available in the cocktail machine) and a "measure" which is the amount of liquid to serve (1 = 2ml, 2 = 4ml, ...).
{
"cocktails": [{
"cocktail": {
"name": "Virgin mojito",
"ingredients": [{
"ingredient": {
"name": "sirop de mojito", "measure": 2
}
}, {
"ingredient": {
"name": "menthe verte",
"measure": 1
}
}, {

"ingredient": {
"name": "jus de citron",
"measure": 1
}
}, {
"ingredient": {
"name": "sucre de canne",
"measure": 1
}
}, {
"ingredient": {
"name": "eau gazeuse",
"measure": 2
}
},
{
"ingredient": {
"name": "glace pilee",
"measure": 1
}
}
]
}
}, {
}]
}
When displaying a cocktail on the web page you can see two columns. A column for the ingredients available in the machine and a column for the ingredients to be added manually.

## 6.5) The web page

Yes but why a web page and not a mobile application? The answer is simple, because it is compatible on all smartphones and PCs.

The web page is accessible at the IP address http://mybar.local/ or http://192.168.1.51 of your network. This is HTML and CSS code generated by the C code of wroom32. When the module starts, the software cycles through the JSON "bottles" and "cocktails" to create a dynamic HTML table with three columns and N line(s). In column one, we have the CSS buttons with the name of the cocktail (available in the JSON). In column two we have the ingredient(s) to add manually (not available in bottle list). In column three we have the ingredient (s) available in the cocktail machine (available in bottle list).

### 6.5.1) The CSS

In the CSS we have buttons, the font, the background color … <style>
h1 {

color: white;
text-align: center;
}
p {
font-family: verdana;
font-size: 20px;
}
body {
background-color: lightblue; }
table
{
border-collapse: collapse; }
td
{
border: 1px solid black;
}
.button {
width:85px;
height:85px;
background:#fafafa;
box-shadow:2px 2px 8px #aaa; font:bold 13px Arial;
border-radius:50%;
color:#555;
}
</style>

### 6.5.1) HTML

In the first line of the HTML code is the title and a link to an image. This line allows, when we add the shortcut of the web page on a smartphone to have a nice shortcut with a name and logo.
<title>Connected bar</title><link
href="https://www.bodipure.com/wp-content
/uploads/2016/09/B-favicon.png" rel="icon" type="image/x-icon" />

The rest of the HTML code is the three-column table. Here is an example below:

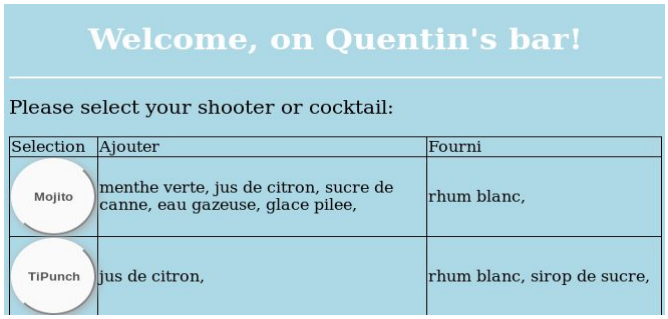
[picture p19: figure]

# 7) Mechanics

## 7.1) The wood

I bought wood and metal brackets at a hardware store. You need a drill, a circular saw, and a screwdriver.

## 7.2) The tray

You can easily make yourself the mechanical tray, however to avoid spending too much time on the realization of this mechanical part I use the 3D plans propose by "DIY Machines" (https://www.thingiverse.com/thing: 2478890/zip).

License:
Robotic Bartender (https://www.thingiverse.com/thing:2478890) by DIY_Machines is licensed under the Creative Commons - Attribution license. http://creativecommons.org/licenses/by/3.0/

# 8) Getting started and functioning

You have to clone the git repository: https://github.com/Mras2an/cocktail-machine

## 8.1) Hardware connection

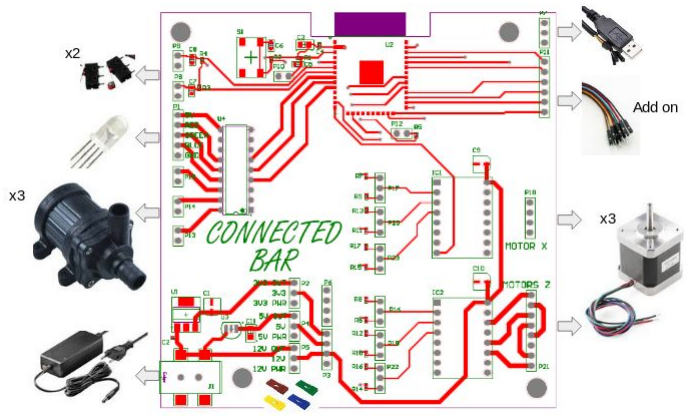
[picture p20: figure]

## 8.2) Configure the software

After soldering your card and building the mechanical part of the system you have to configure some parameters.
1 - Board.h
Used to define the GPIO mapping of the system. Example for the RGB LED:
#define LED_GPIO_RED | BAR_GPIO_NUM_32

#define LED_GPIO_GREEN | BAR_GPIO_NUM_33

#define LED_GPIO_BLUE | BAR_GPIO_NUM_25

1 - the motors
you have to modify the "#define" of Motor.c to calibrate the number of steps according to the mechanics of the cocktail machine.

2 - The JSON
You have to bring in your bottles and create your cocktail.

## 8.3) Compile and program the code

1 - In a GNU / Linux terminal do an export of the SDK-IDF (branch 2.1) and the toolchain. $ export IDF_PATH=/YOUR_PATH/esp-idf
$ export PATH=$PATH:/YOUR_PATH/xtensa-esp32-elf/bin/

2 - In the project make a "make"

3 - Connect the card with the jumper Boot. Then use the espressif flashing software. $ python /esptool.py --chip esp32 --port /dev/ttyUSB0 --baud 115200 --before default_reset --after hard_reset write_flash -z --flash_mode dio --flash_freq 40m --flash_size detect 0x1000 bootloader.bin 0x10000 cocktail-machine.bin 0x8000 customPart.bin

4 - Now you can use OTA functionality to update your system (you have to be connected to your home wi-fi). For that go to the web page (http://mybar.local/ or http://192.168.1.51) and click on the button "Update" at the end of the page (the LED is green). Go to utils file and execute the command follow:
$ python update_firmware.py 192.168.1.51 cocktail-machine.bin

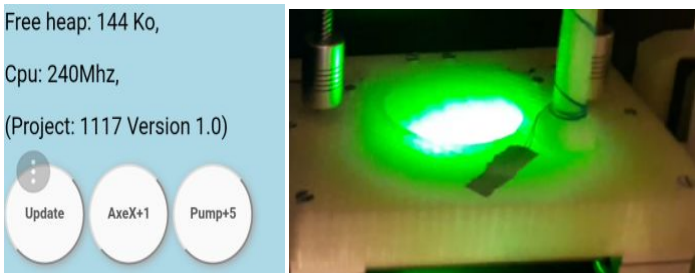
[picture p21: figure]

## 8.4) First boot

1 - At start-up the LED is red, the Y-axis searches for the end position, then the X-axis searches for the end position. Once the system is initialized the LED goes blue.

2 - When you start the system for the first time, connect the system to your Wi-Fi box. To do this download the application "ESP8266 SmartConfig" on your phone's awning. Connect your phone to your wifi, and launch the espressif application. You just have to enter your wifi password and click on "confirm". The module will save in flash your SSID and password. Once saved the smartconfig mode will be disabled at startup.

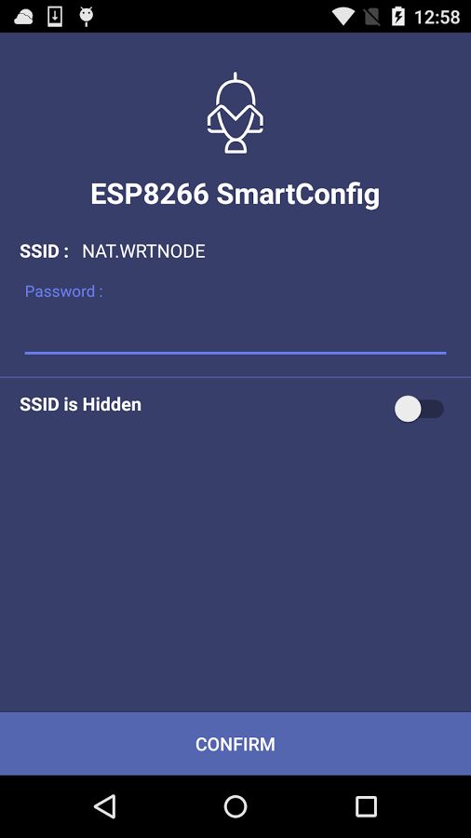
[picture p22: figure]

3 - Go to http://mybar.local/ or http://192.168.1.51 and choose your cocktail.

4 - Enjoy :-)

## 8.4) Movies

You can watch videos on my youtube channel: https://www.youtube.com/watch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

## 8.5) Hygiene of the cocktail machine

For good hygiene, remember to clean the machine after each bottle switch.

# 9) The future of the project

The version presented is the version 1. Many things remain to be modified and added

## 9.1) Modify

- Be careful, on my board (PCB) I switch the 5v in 12v on the ULN2803 but you can use the 5 volts if you want.

## 9.2) Add

- Detection of the glass.

# 10) Pictures

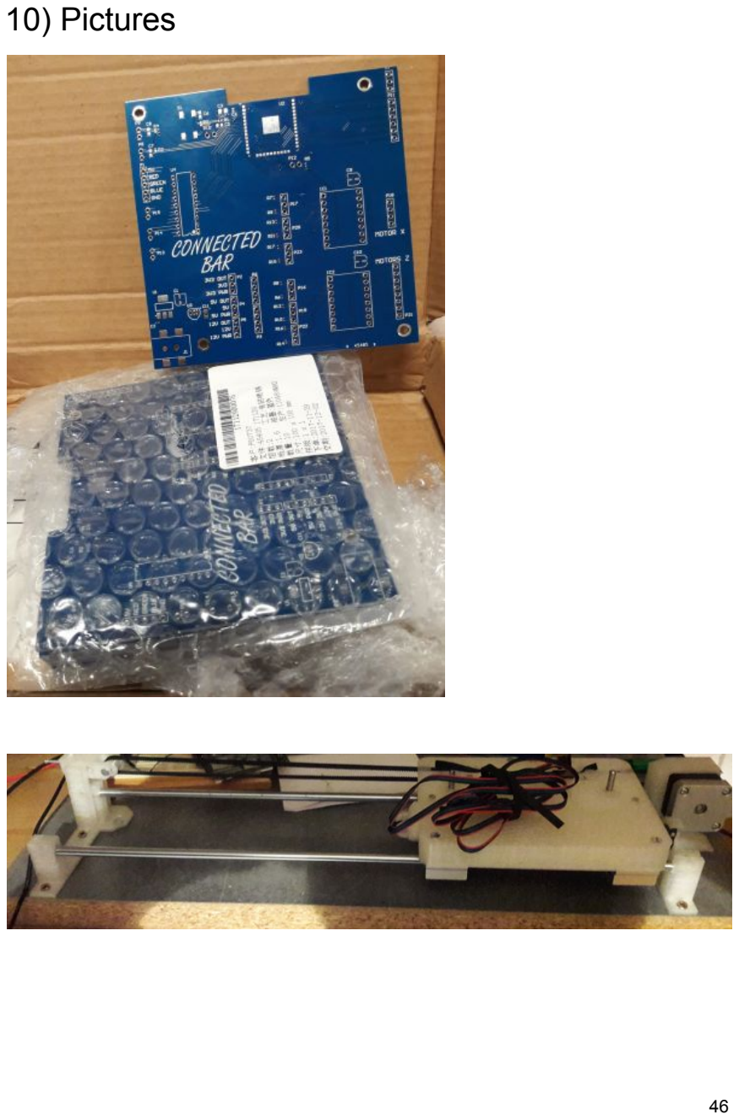
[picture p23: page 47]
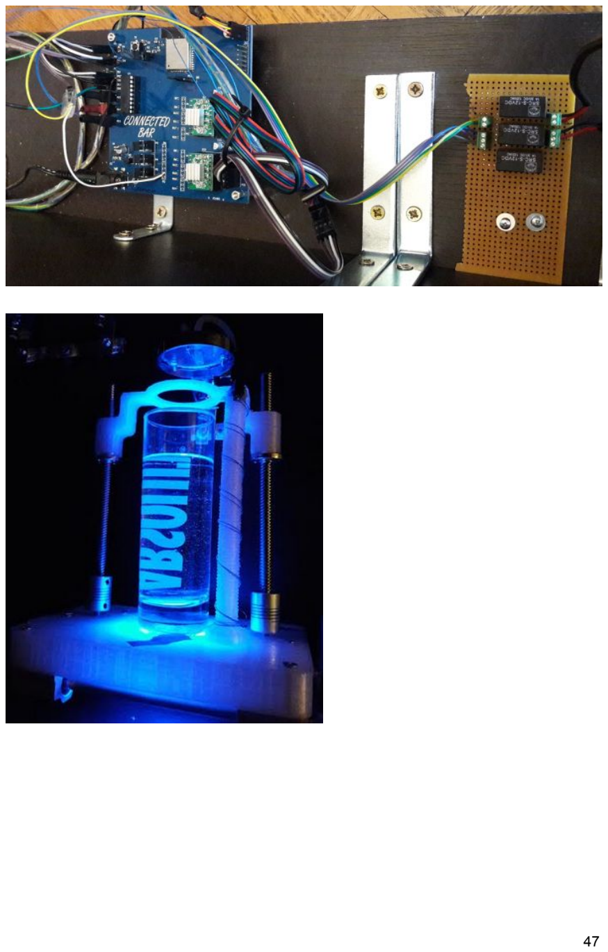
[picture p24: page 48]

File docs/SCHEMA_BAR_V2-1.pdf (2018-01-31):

Title; Size; Number; Revision; Date:; Sheet of; File:; E:\PROJETS\..\BAR_TENDER_ARCHITECTURE.SchDoc Drawn By:; ESP32_GPIO12; ESP32_GPIO13; ESP32_GPIO14; ESP32_GPIO15; ESP32_GPIO23; Designator; BAR_TENDER_QUENTIN.SchDoc

Designator
MOTOR DRIVERS.SchDoc


D D

C C

B B

A A

Title

File: E:\PROJETS\..\BAR_TENDER_QUENTIN.SchDoc Drawn By:

GPIO26/DAC_2/ADC2_CH9/RTC_GPIO7/EMAC_RXD1 11

GPIO10/SD_DATA3/SPIWP/HS1_DATA3/U1TXD 18

GPIO33/XTAL_32K_N/ADC1_CH5/TOUCH8/RTC_GPIO8 9

GPIO12/ADC2_CH5/TOUCH5/RTC_GPIO15/MTDI/HSPIQ/HS2_DATA2/SD_DATA2/EMAC_TX3 14

GPIO9/SD_DATA2/SPIHD/HS1_DATA2/U1RXD 17

GPIO13/ADC2_CH4/TOUCH4/RTC_GPIO14/MTCK/HSPID/HS2_DATA3/SD_DATA3/EMAC_RX_ER 16

GPIO25/DAC_1/ADC2_CH8/RTC_GPIO6/EMAC_RXD0 10

GPIO36/SENSOR_VP/ADC_H/ADC1_CH0/RTC_GPIO0 4

EN 3 | 3V³

2

GPIO14/ADC2_CH6/TOUCH6/RTC_GPIO16/MTMS/HSPICLK/HS2_CLK/SD_CLK/EMAC_TX2 13

GPIO39/SENSOR_VN/ADC1_CH3/ADC_H/RTC_GPIO3 5

GPIO32/XTAL_32K_P/ADC1_CH4/TOUCH9/RTC_GPIO9 8

GPIO34/ADC1_CH6/RTC_GPIO4 6
GPIO35/ADC1_CH7/RTC_GPIO5 7 | GND¹

1

GPIO27/ADC2_CH7/TOUCH7/RTC_GPIO17/EMAC_RX_DV 12 | GND_2 15

GPIO11/SD_CMD/SPICS0/HS1_CMD/U1RTS 19 GPIO6/SD_CLK/SPICLK/HS1_CLK/U1CTS 20

GPIO5/VSPICS0/HS1_DATA6/EMAC_RX_CLK | 29
GPIO15/ADC2_CH3/TOUCH3/MTD0/HSPICS0/RTC_GPIO13/HS2_CMD/SD_CMD/EMAC_RXD3 | 23
GPIO19/VSPIQ/U0CTS/EMAC_TXD0 | 31
GPIO4/ADC2_CH0/TOUCH0/RTC_GPIO10/HSPIHD/HS2_DATA1/SD_DATA1/EMAC_TX_ER | 26
GPIO2/ADC2_CH2/TOUCH2/RTC_GPIO12/HSPIWP/HS2_DATA0/SD_DATA0 | 24
GPIO0/ADC2_CH1/TOUCH1/RTC_GPIO11/CLK_OUT1/EMAC_TX_CLK | 25
GPIO18/VSPICLK/HS1_DATA7 | 30
GPIO22/VSPIWP/U0RTS/EMAC_TXD1 | 36
GPIO23/VSPID/HS1_STROBE | 37
GPIO16/HS1_DATA4/U2_RXD/EMAC_CLK_OUT | 27
GPIO1/U0TXD/CLK_OUT3/EMAC_RXD2 | 35
NC | 32
GPIO3/U0RXD/CLK_OUT2 | 34
GPIO21/VSPIHD/EMAC_TX_EN | 33
GPIO17/HS1_DATA5/U2_TXD/EMAC_CLK_OUT_180 | 28
GPIO8/SD_DATA1/SPID/HS1_DATA1/U2CTS | 22
GPIO7/SD_DATA0/SPIQ/HS1_CLK/U2RTS | 21 GND_3 38 | GND_EP 39

U2

GND

PWR | 3V3_OUT GND

2

VOUT | 3 VIN 1 | GND

4

U1

GND

47uF

C1

1uF

C2

ESP32-Rx

ESP32-Tx

3V3

100nF

C4

GND

10uF

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
ESP32-Rx

ESP32-Tx

GND

Reset

GND

1

1

2

2

P10

Reset

3V3

10K

R1

100nF

C5

GND

Boot

Boot

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
Switch_GLASS_DETECTION

1 34 2 S1

GND

10K

R2

3V3

Switch_MODE

100nF

C6

Switch_STOP_DETECTION

LED_BLUE
PUMP_1

PUMP_1_OUT 1

1

2

2

P13

PUMP_2_OUT 1

1

2

2

P14

PUMP_2

PUMP_3

LED_RED
LED_GREEN

Switch_MODE

GND

1

1

2

2

P9

Switch_GLASS_DETECTION | Switch_STOP_DETECTION

IN 1 1

IN 8 8

IN 2 2

IN 3 3

IN 4 4

IN 5 5

IN 6 6

IN 7 7

GND 9 | COM | 10
| OUT 8 | 11
OUT 7 | 12
OUT 6 | 13
OUT 5 | 14
OUT 4 | 15
OUT 3 | 16
OUT 2 | 17
OUT 1 | 18

U4
GND
PUMP_1 | PUMP_1_OUT
| PUMP_2_OUT
| PUMP_3_OUT

PUMP_2

PUMP_3

LED_GREEN

LED_RED

LED_BLUE

LED_GREEN_OUT

LED_RED_OUT

LED_BLUE_OUT

PUMP_3_OUT 1

1

2

2

P15

3V3

10K

R4

100nF

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
100nF

C7

SPARE 1

SPARE 2

SPARE 3
SPARE 4
SPARE 5

SPARE 6

SPARE 5

SPARE 6

SPARE 3

SPARE 4

SPARE 1

SPARE 2

1

1

2

2

3

3

P2

3V3_OUT

3V3

3V3_PWR

1

1

2

2

3

3

P4

5V_OUT

5V

5V_PWR

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
12V_PWR

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
3V3_PWR

GND

12V_PWR

5V_PWR

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
5V GND

2

VOUT 1 VIN 3

U3

PWR | 5V_OUT

GND

10uF

C11

J1

LD-0223-T25

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
LED_GREEN_OUT

LED_RED_OUT

LED_BLUE_OUT

GND

ESP32_GPIO15

ESP32_GPIO14
ESP32_GPIO12
ESP32_GPIO13

1

1

2

2

3

3

P11

ESP32_GPIO23

12V

12V

12V

12V

12V


D D

C C

B B

A A

Title

File: E:\PROJETS\..\MOTOR DRIVERS.SchDocDrawn By:

MS3_1

MS2_1

MS1_1

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
MS3_2

MS2_2

MS1_2

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
MS3_1

MS2_1

MS1_1

47uF

C9

GND

MOTOR X

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
P18 ESP32_GPIO13
ESP32_GPIO12

GND

3V3

MS3_2

MS2_2

MS1_2

47uF

C10

GND

MOTOR Z

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
2B_2
2A_2
1A_2
1B_2

2B_2

2A_2

1A_2

1B_2

MOTORZ_2

MOTORZ_2

MOTORZ_4

MOTORZ_4

ESP32_GPIO15
ESP32_GPIO14

ENA 1
MS1 2
MS2 3
MS3 4
RESET 5
SLEEP 6
STEP 7
DIR 8 | GND | 9
| VDD | 10
| 1B | 11
1A | 12
2A | 13
2B | 14
GND | 15
VMOT | 16

IC1

ENA 1
MS1 2
MS2 3
MS3 4
RESET 5
SLEEP 6
STEP 7
DIR 8 | GND | 9
| VDD | 10
| 1B | 11
1A | 12
2A | 13
2B | 14
GND | 15
VMOT | 16

IC2

ESP32_GPIO23

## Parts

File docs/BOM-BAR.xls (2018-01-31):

Comment | Description | Designator | Footprint | LibRef | Quantity
EEEFK0J470UR | CAP 47uF 6.3V ALU CMS | C1, C9, C10 | CAPA CHIMIQUE CMS | EEEFK0J470UR | 3.0
GRM155R60J105KE19D | CAP 1UF 6V3 X5R CER 0402 CMS | C2 | 0402 | GRM155R60J105KE19D | 1.0
0805YD106KAT2A | CAP 10uF 16V X5R CER 0805 CMS | C3, C11 | 0805 POLARISE | 0805YD106KAT2A | 2.0
CC0402KRX7R6BB104 | CAP 100NF K10V X7R CER 0402 CMS | C4 | 0402 | CC0402KRX7R6BB104 | 1.0
MC0603B104K250CT | CAP 100NF 25V X7R CER 0603 CMS | C5, C6, C7, C8 | 0603 | MC0603B104K250CT | 4.0
A4988 | MOTOR DRIVER | IC1, IC2 | DRIVER MOTEUR | A4988 | 2.0
LD-0223-T25 | CMS JACK SOCKET PLUG | J1 | PJACK-LIHSHENG-LD-0223-25 | LD-0223-T25 | 1.0
HEADER 1x5 | EMBASE MALE 1 RANGEE VERT 5 VOIES | P1 | EMBASE 5 VOIES | HEADER 1x5 | 1.0
HEADER 1x3 | EMBASE MALE 1 RANGEE VERT 3VOIES | P2, P4, P5, P7, P16, P17, P19, P20, P22, P23 | EMBASE 3 VOIES | HEADER 1x3 | 10.0
HEADER 1x4 | EMBASE MALE 1 RANGEE VERT 4 VOIES | P3, P6, P18 | EMBASE 4 VOIES | HEADER 1x4 | 3.0
HEADER 1x2 | EMBASE MALE 1 RANGEE VERT 2 VOIES 2.54mm | P8, P9, P10, P12, P13, P14, P15 | EMBASE 2 VOIES - 2.54mm | HEADER 1x2 - 2.54 mm | 7.0
HEADER 1x6 | EMBASE MALE 1 RANGEE VERT 6 VOIES | P11 | EMBASE 6 VOIES - VERTICAL | HEADER 1x6 | 1.0
HEADER 1x8 | EMBASE MALE 1 RANGEE VERT 8 VOIES | P21 | EMBASE 8 VOIES - VERTICAL | HEADER 1x8 | 1.0
MC 0.0625W 0402 1% 10K | RESIST.CMS 0402 1/16W 5% 10K | R1, R2, R3, R4, R5, R6, R7, R8, R9, R10, R11, R12, R13, R14, R15, R16, R17 | 0402 | MC 0.0625W 0402 1% 10K | 17.0
Switch | SWITCH TACTILE | S1 | TACT SWITCH 6X6 | DTSM-61R-V-* | 1.0
LM3940IMP-3.3/NOPB | REGULATEUR LINEAIRE 3V3 | U1 | SOT-223 | LM3940IMP-3.3/NOPB | 1.0
ESP-WROOM-32 | MODULE WIFI ESPRESSIF WROOM 32 | U2 | MODULE_WIFI ESPRESSIF WROOM 32 | ESP WROOM 32 | 1.0
LM78L05ACZ/NOPB | REGULATEUR LINEAIRE 5V | U3 | TO-92 | LM78L05ACZ/NOPB | 1.0
ULN2803A | Transistor en réseau bipolaire | U4 | DIP 18 | ULN2803A | 1.0

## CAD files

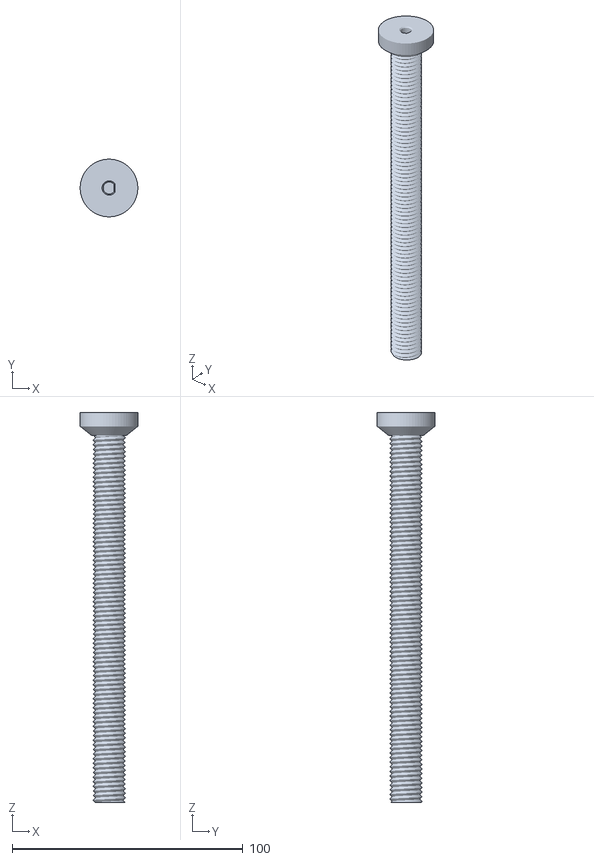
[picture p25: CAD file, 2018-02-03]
docs/3D files/files/main_rod2.3.STL
25.0 x 25.0 x 169.0

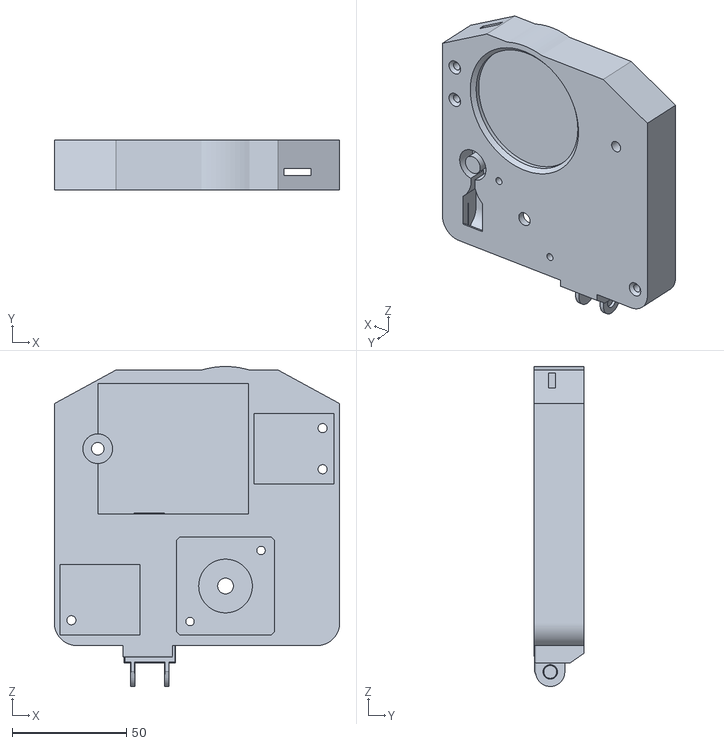
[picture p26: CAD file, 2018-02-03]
docs/3D files/files/Slider_Base_V3_-_P1of2.STL
125.0 x 22.0 x 140.1

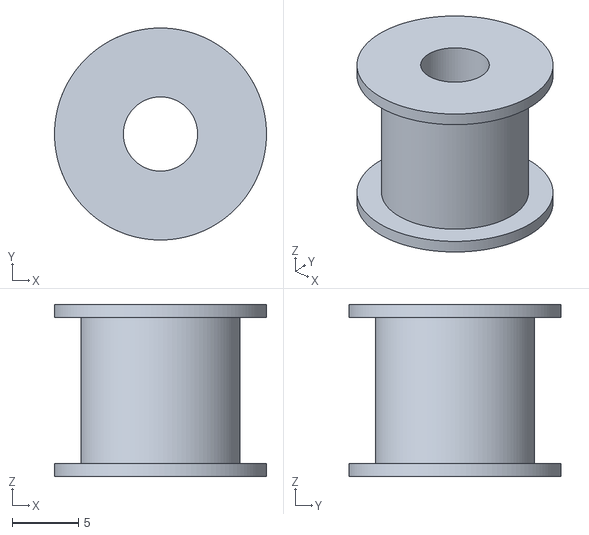
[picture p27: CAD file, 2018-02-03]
docs/3D files/files/Idler.STL
16.0 x 16.0 x 13.0

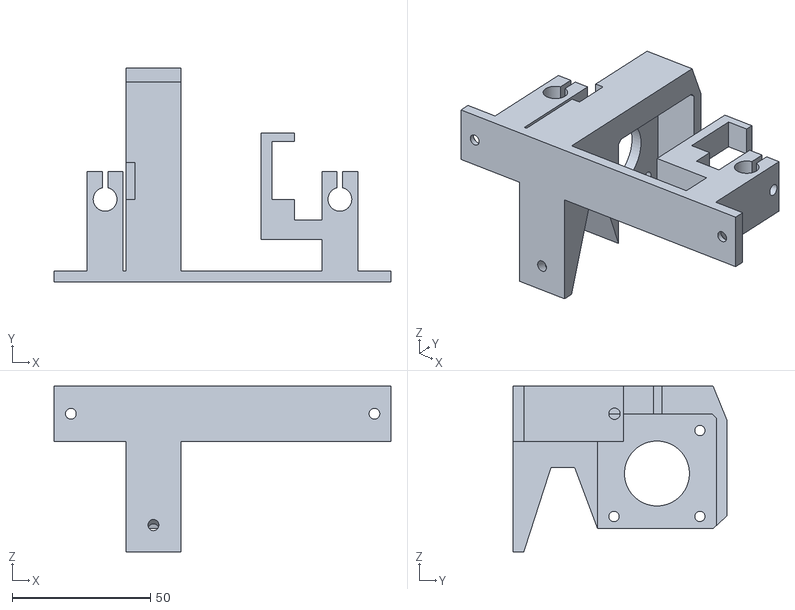
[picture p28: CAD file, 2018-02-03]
docs/3D files/files/X_Axis_Motor_Mount.STL
122.0 x 77.6 x 60.0

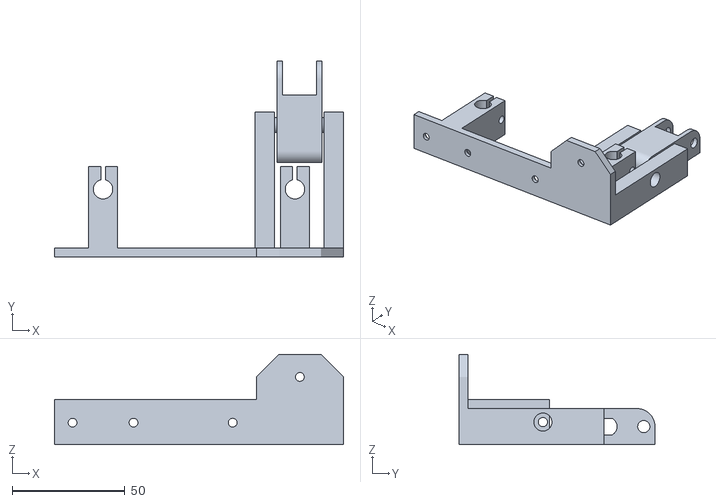
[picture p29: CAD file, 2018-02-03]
docs/3D files/files/Rod_Clamp_V5.STL
128.0 x 86.8 x 40.0

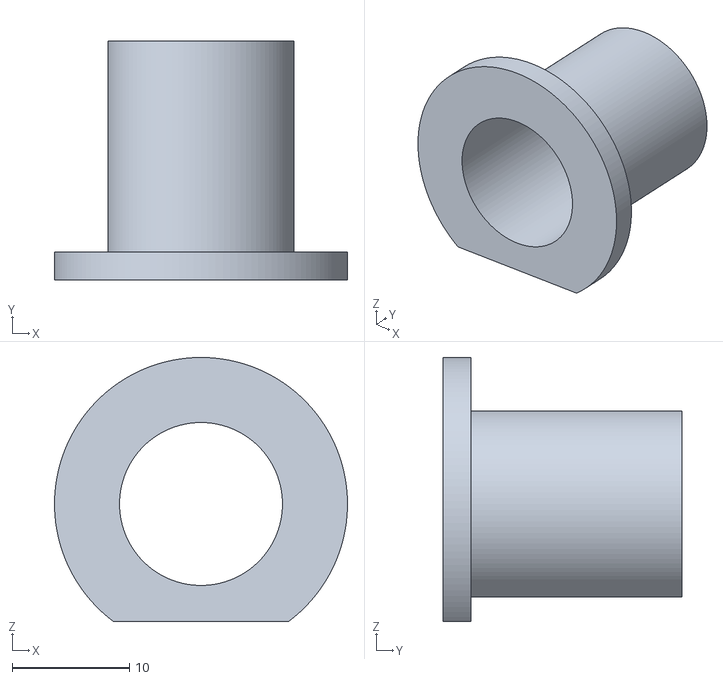
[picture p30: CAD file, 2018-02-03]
docs/3D files/files/Table_Tidy.STL
25.0 x 20.4 x 22.5

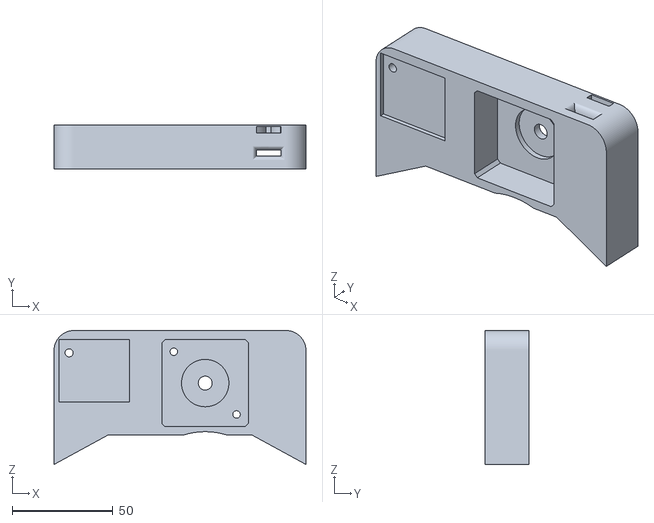
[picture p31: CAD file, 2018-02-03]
docs/3D files/files/Slider_Base_V3_-_P2of2.STL
125.0 x 22.0 x 66.5

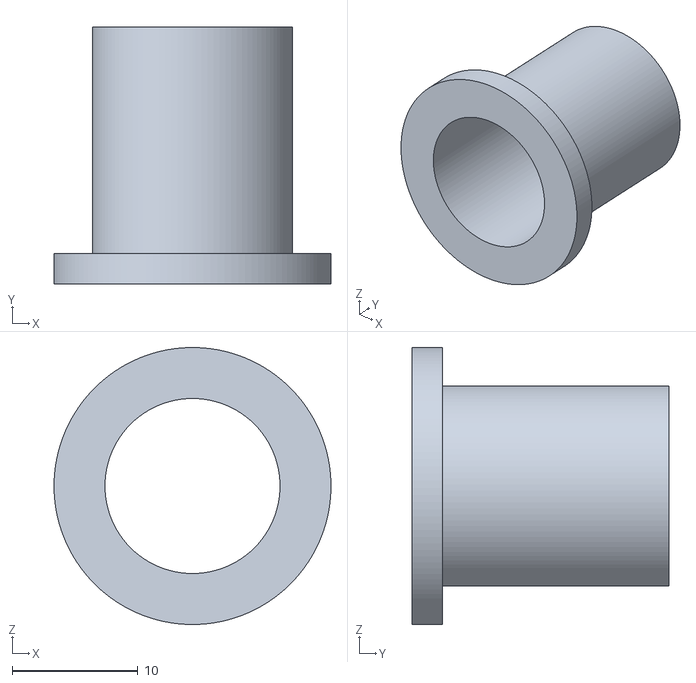
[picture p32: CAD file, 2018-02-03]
docs/3D files/files/Table_Tidy_End.STL
22.0 x 20.4 x 22.0

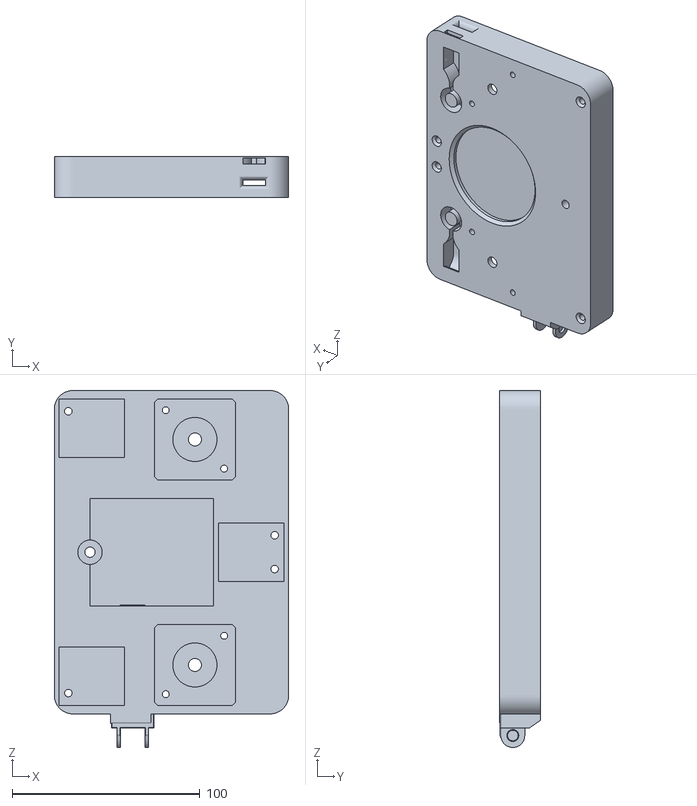
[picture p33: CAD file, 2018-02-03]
docs/3D files/files/Slider_Base_V3.STL
125.0 x 22.0 x 190.3

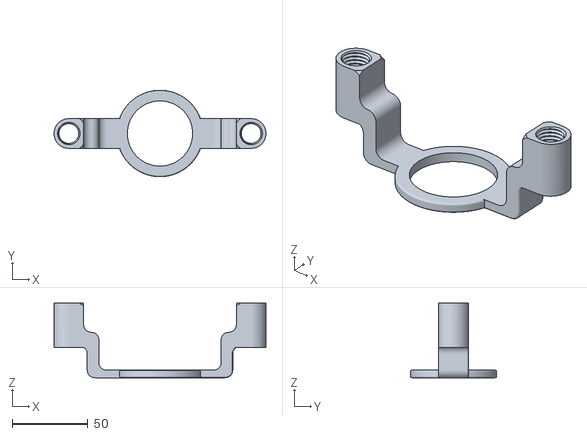
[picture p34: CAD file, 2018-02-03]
docs/3D files/files/Dispensor_Paddle_V2.STL
139.8 x 57.0 x 49.1

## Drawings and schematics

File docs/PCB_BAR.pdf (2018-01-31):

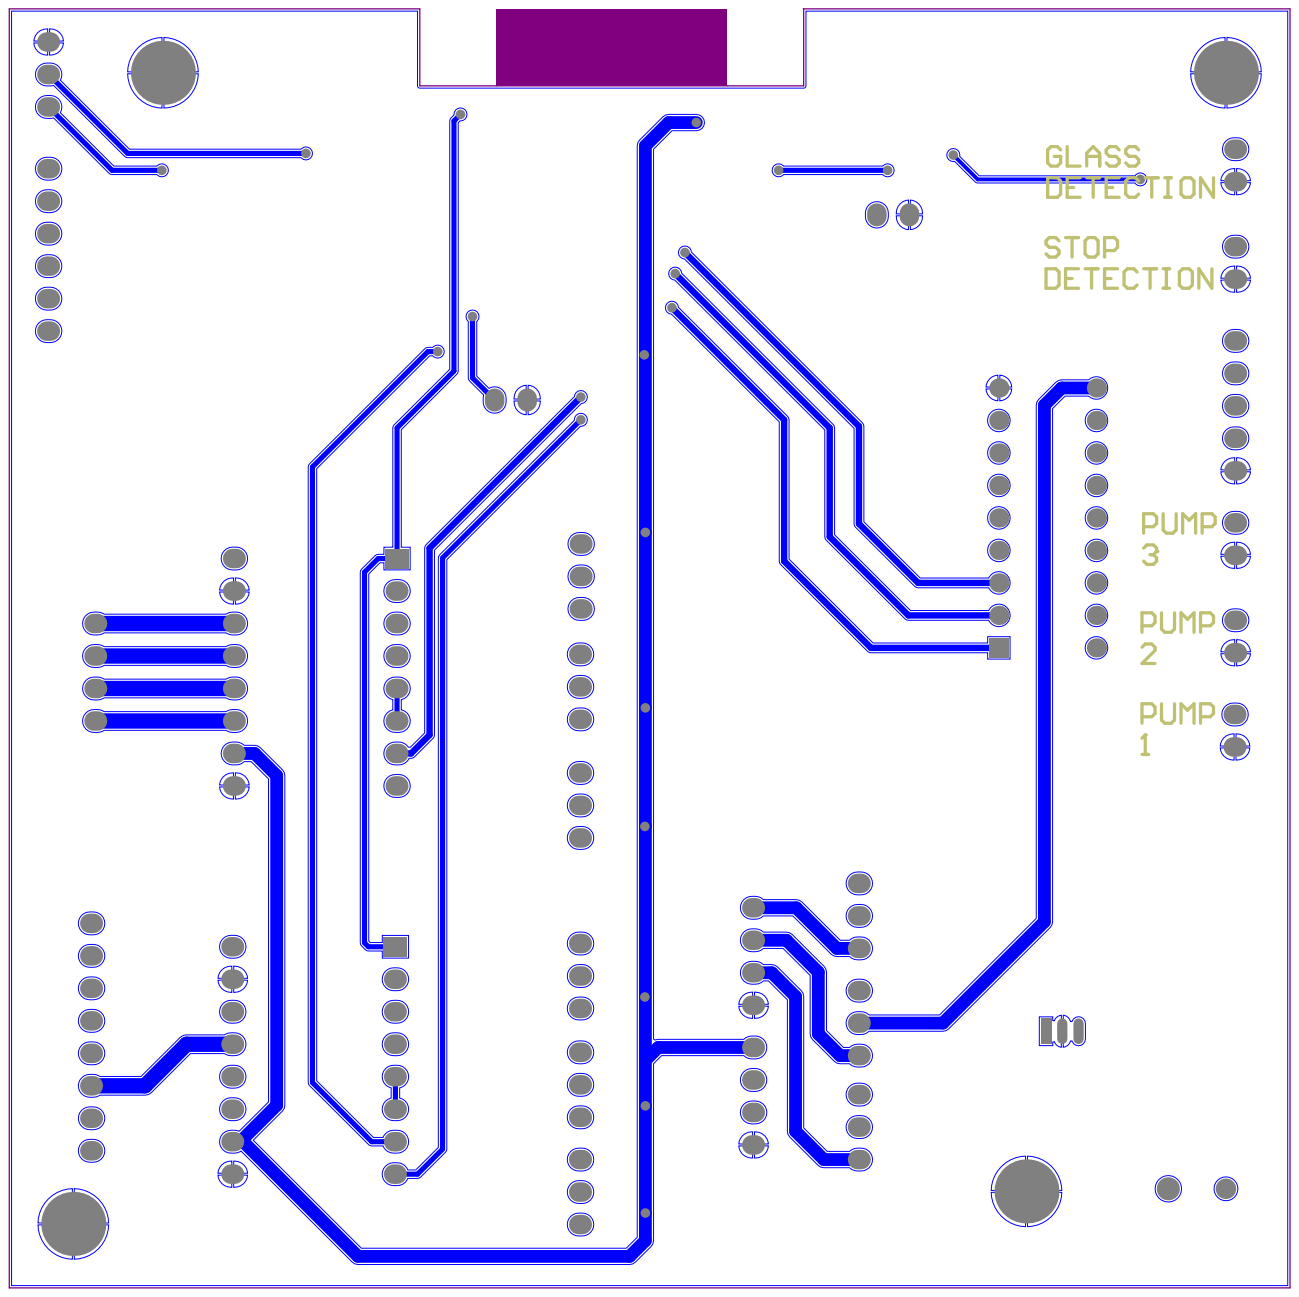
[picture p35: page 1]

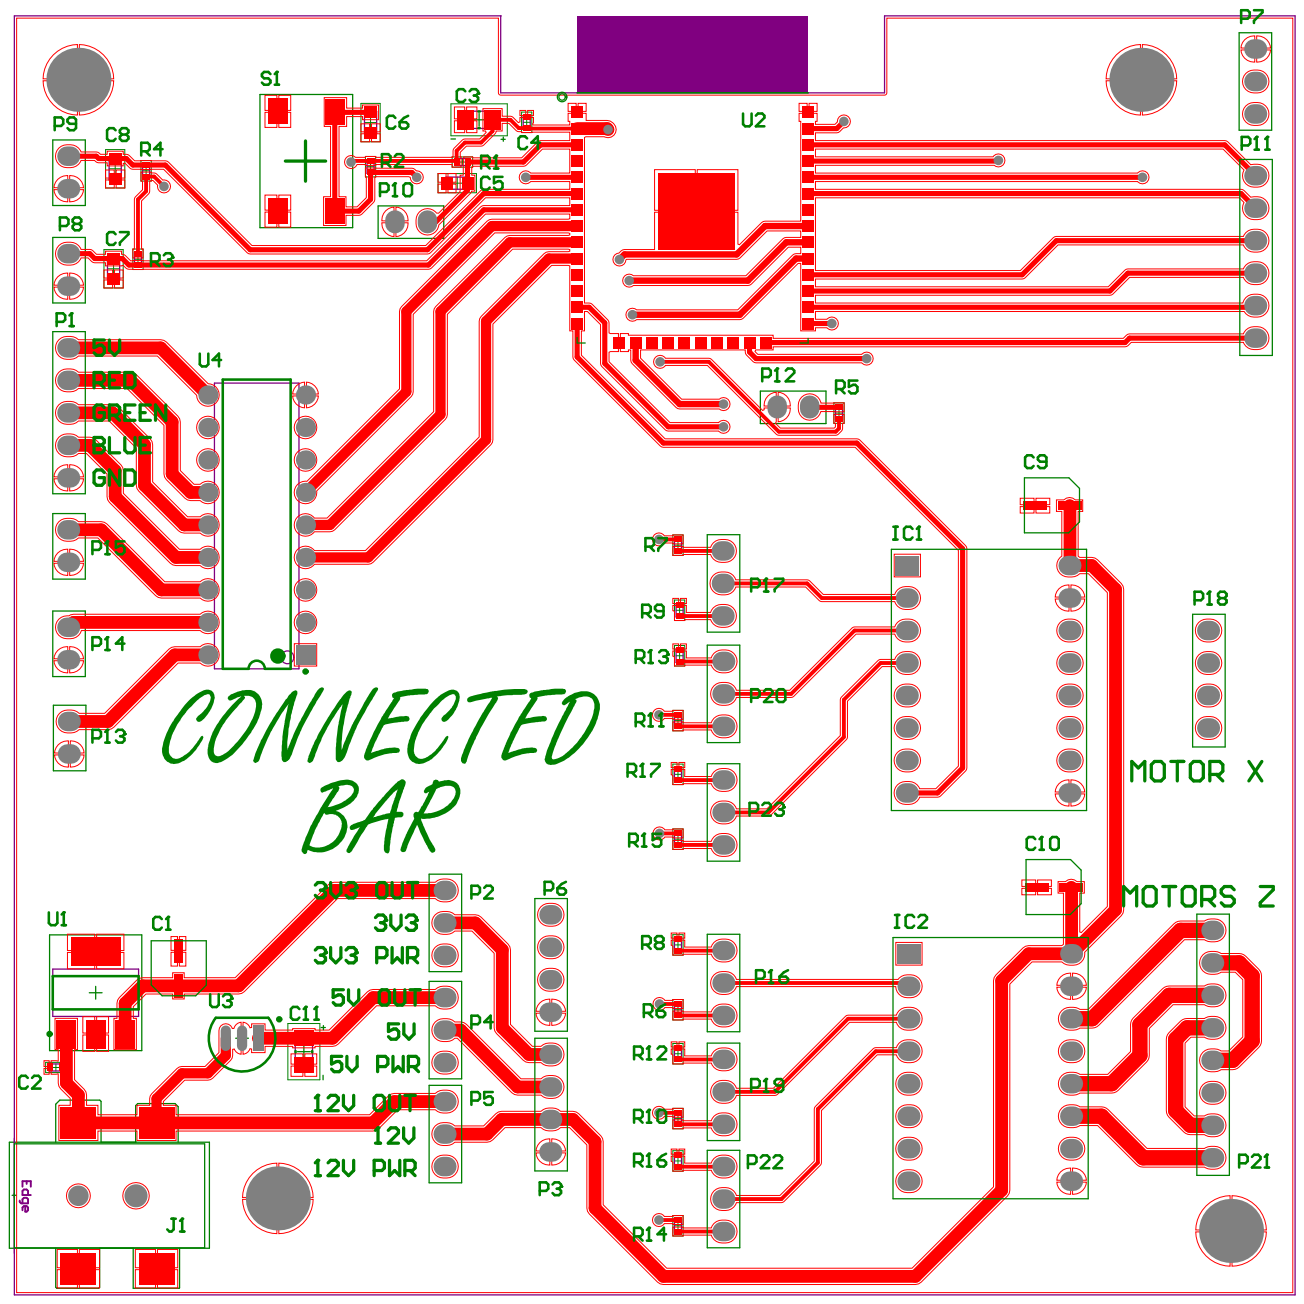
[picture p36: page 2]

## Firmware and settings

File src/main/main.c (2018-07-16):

#include "Wifi.h"
#include "System.h"
#include "Initialize.h"
#include "Board.h"
#include "ButtonHandling.h"
#include "LedRGBHandling.h"
#include "Html.h"
#include "CpuDelay.h"
#include "Gpio.h"
#include "MotorHandling.h"

#ifdef SMART_CONFIG
    #include "SmartConfig.h"
#endif

/******************************************************************************
 * FunctionName : void app_main(void)
 * Parameters   : void
 * Returns      : void
 *******************************************************************************/
void app_main(void)
{
    /* gpio switch stop detection*/
    BAR_ERROR_CHECK(Gpio_configure(DETECTION_AXE_X, BAR_GPIO_MODE_INPUT, BAR_GPIO_PULL_NONE));
    /* gpio switch stop detection*/
    BAR_ERROR_CHECK(Gpio_configure(DETECTION_AXE_Y, BAR_GPIO_MODE_INPUT, BAR_GPIO_PULL_NONE));
    Initialize_init();
    BarDebug_info("Free Heap at %d = %d\n", __LINE__, OsGetFreeHeapSize());
    System_init();
    //  BAR_ERROR_CHECK(Gpio_configure(BUTTON_GPIO_MODE, BAR_GPIO_MODE_INPUT, BAR_GPIO_PULL_NONE));
    //  uint32_t bp[1];
    //  Gpio_get(BUTTON_GPIO_MODE, bp);
    //  if(bp[0] == 0)
    //  {
    //    SmartConfig_factoryReset();
    //  }
    #ifdef SMART_CONFIG
    SmartConfig_init();
    #endif
    Wifi_init();
    BarDebug_info("Free Heap at %d = %d\n", __LINE__, OsGetFreeHeapSize());
}

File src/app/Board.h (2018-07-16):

#ifndef _BOARD_H_
#define _BOARD_H_

#include "Gpio.h"

#ifdef ESP32
    #define LED_GPIO_RED            BAR_GPIO_NUM_32
    #define LED_GPIO_GREEN          BAR_GPIO_NUM_33
    #define LED_GPIO_BLUE           BAR_GPIO_NUM_25

    #define MOTOR_AXE_X_DIR         BAR_GPIO_NUM_12
    #define MOTOR_AXE_X_CLK         BAR_GPIO_NUM_13
    #define MOTOR_AXE_Y_DIR         BAR_GPIO_NUM_14
    #define MOTOR_AXE_Y_CLK         BAR_GPIO_NUM_15

    #define MOTOR_PUMP_1            BAR_GPIO_NUM_5
    #define MOTOR_PUMP_2            BAR_GPIO_NUM_18
    #define MOTOR_PUMP_3            BAR_GPIO_NUM_19

    #define DETECTION_AXE_Y         BAR_GPIO_NUM_34
    #define DETECTION_AXE_X         BAR_GPIO_NUM_35

    #define BUTTON_GPIO_MODE        BAR_GPIO_NUM_39
#else
    #error "board/hardware is not defined"
#endif


#endif /* _BOARD_H_ */

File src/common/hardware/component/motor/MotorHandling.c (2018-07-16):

#include <stdio.h>
#include "CpuDelay.h"
#include "Gpio.h"
#include "MotorHandling.h"
#include "Board.h"

//#define MOTOR_OFFSET 200 //360°
#define MOTOR_OFFSET 495   //10cm
#define MOTOR_LIMIT 800

/******************************************************************************
 * FunctionName : void MotorHandling_init(void)
 * Parameters   : none
 * Returns      : none
 *******************************************************************************/
void MotorHandling_init(void)
{
    //x
    BAR_ERROR_CHECK(
        Gpio_configure(MOTOR_AXE_X_DIR, BAR_GPIO_MODE_INPUT_OUTPUT, BAR_GPIO_PULL_NONE));
    BAR_ERROR_CHECK(
        Gpio_configure(MOTOR_AXE_X_CLK, BAR_GPIO_MODE_INPUT_OUTPUT, BAR_GPIO_PULL_NONE));
    //y
    BAR_ERROR_CHECK(
        Gpio_configure(MOTOR_AXE_Y_DIR, BAR_GPIO_MODE_INPUT_OUTPUT, BAR_GPIO_PULL_NONE));
    BAR_ERROR_CHECK(
        Gpio_configure(MOTOR_AXE_Y_CLK, BAR_GPIO_MODE_INPUT_OUTPUT, BAR_GPIO_PULL_NONE));
    // pump
    BAR_ERROR_CHECK(
        Gpio_configure(MOTOR_PUMP_1, BAR_GPIO_MODE_INPUT_OUTPUT, BAR_GPIO_PULL_NONE));
    BAR_ERROR_CHECK(
        Gpio_configure(MOTOR_PUMP_2, BAR_GPIO_MODE_INPUT_OUTPUT, BAR_GPIO_PULL_NONE));
    BAR_ERROR_CHECK(
        Gpio_configure(MOTOR_PUMP_3, BAR_GPIO_MODE_INPUT_OUTPUT, BAR_GPIO_PULL_NONE));
}

/******************************************************************************
 * FunctionName : void MotorHandling_setPositionOnX(int position)
 * Parameters   : int
 * Returns      : none
 *******************************************************************************/
void MotorHandling_setPositionOnX(int position)
{
    if(position == 0) {
        MotorHandling_setInitialPosition();
        return;
    }

    int end = 0;

    if(position > 0) {
        BAR_ERROR_CHECK(Gpio_set(MOTOR_AXE_X_DIR, BAR_LEVEL_LOW));
        end = position * MOTOR_OFFSET;
    } else {
        BAR_ERROR_CHECK(Gpio_set(MOTOR_AXE_X_DIR, BAR_LEVEL_HIGH));
        end = (position * (-1)) * MOTOR_OFFSET;
    }

    //  uint32_t bp1[1];
    for(int i = 0; i < end; i++) {
        BAR_ERROR_CHECK(Gpio_set(MOTOR_AXE_X_CLK, BAR_LEVEL_LOW));
        CpuDelay_ms(1);
        BAR_ERROR_CHECK(Gpio_set(MOTOR_AXE_X_CLK, BAR_LEVEL_HIGH));
        CpuDelay_ms(1);
        //    if (position < 0)
        //    {
        //      Gpio_get(DETECTION_AXE_X, bp1);
        //      if (!bp1[0]) {
        //          BarDebug_info("Stop motor.\n");
        //        break;
        //      }
        //    }
    }
}

/******************************************************************************
 * FunctionName : static void MotorHandling_get10ml()
 * Parameters   : none
 * Returns      : none
 *******************************************************************************/
static void MotorHandling_get10ml()
{
    int end = MOTOR_LIMIT;
    BAR_ERROR_CHECK(Gpio_set(MOTOR_AXE_Y_DIR, BAR_LEVEL_LOW));

    for(int i = 0; i < end; i++) {
        BAR_ERROR_CHECK(Gpio_set(MOTOR_AXE_Y_CLK, BAR_LEVEL_LOW));
        CpuDelay_ms(1);
        BAR_ERROR_CHECK(Gpio_set(MOTOR_AXE_Y_CLK, BAR_LEVEL_HIGH));
        CpuDelay_ms(1);
    }

    CpuDelay_ms(600);
    uint32_t bp2[1];
    Gpio_get(DETECTION_AXE_Y, bp2);
    BAR_ERROR_CHECK(Gpio_set(MOTOR_AXE_Y_DIR, BAR_LEVEL_HIGH));
    end = MOTOR_LIMIT;

    while(bp2[0] && (end != 0)) {
        Gpio_get(DETECTION_AXE_Y, bp2);
        BAR_ERROR_CHECK(Gpio_set(MOTOR_AXE_Y_CLK, BAR_LEVEL_LOW));
        CpuDelay_ms(1);
        BAR_ERROR_CHECK(Gpio_set(MOTOR_AXE_Y_CLK, BAR_LEVEL_HIGH));
        CpuDelay_ms(1);
        end--;
    }

    CpuDelay_ms(800);
}

/******************************************************************************
 * FunctionName : static void MotorHandling_get25ml()
 * Parameters   : void
 * Returns      : none
 *******************************************************************************/
static void MotorHandling_get25ml()
{
    int end = MOTOR_LIMIT;
    BAR_ERROR_CHECK(Gpio_set(MOTOR_AXE_Y_DIR, BAR_LEVEL_LOW));

    for(int i = 0; i < end; i++) {
        BAR_ERROR_CHECK(Gpio_set(MOTOR_AXE_Y_CLK, BAR_LEVEL_LOW));
        CpuDelay_ms(1);
        BAR_ERROR_CHECK(Gpio_set(MOTOR_AXE_Y_CLK, BAR_LEVEL_HIGH));
        CpuDelay_ms(1);
    }

    CpuDelay_ms(2000);
    uint32_t bp2[1];
    Gpio_get(DETECTION_AXE_Y, bp2);
    BAR_ERROR_CHECK(Gpio_set(MOTOR_AXE_Y_DIR, BAR_LEVEL_HIGH));
    end = MOTOR_LIMIT;

    while(bp2[0] && (end != 0)) {
        Gpio_get(DETECTION_AXE_Y, bp2);
        BAR_ERROR_CHECK(Gpio_set(MOTOR_AXE_Y_CLK, BAR_LEVEL_LOW));
        CpuDelay_ms(1);
        BAR_ERROR_CHECK(Gpio_set(MOTOR_AXE_Y_CLK, BAR_LEVEL_HIGH));
        CpuDelay_ms(1);
        end--;
    }

    CpuDelay_ms(800);
}

/******************************************************************************
 * FunctionName : void MotorHandling_getAMeasureOnY(int measure)
 * Parameters   : int
 * Returns      : none
 *******************************************************************************/
void MotorHandling_getAMeasureOnY(int measure)
{
    BarDebug_info("\t\t MotorHandling_getAMeasureOnY \n");

    if(measure == 1) {
        MotorHandling_get10ml();
    }

    if(measure == 2) {
        MotorHandling_get25ml();
    }

    if(measure == 3) {
        MotorHandling_get25ml();
        MotorHandling_get10ml();
    }

    if(measure == 4) {
        MotorHandling_get25ml();
        MotorHandling_get25ml();
    }

    if(measure == 5) {
        MotorHandling_get25ml();
        MotorHandling_get25ml();
        MotorHandling_get10ml();
    }
}

/******************************************************************************
 * FunctionName : void MotorHandling_getAMeasureOnPump(int measure, int pump)
 * Parameters   : int
 * Parameters   : int
 * Returns      : none
 *******************************************************************************/
void MotorHandling_getAMeasureOnPump(int measure, int pump)
{
    BarDebug_info("\t\t MotorHandling_getAMeasureOnPump \n");
    BAR_ERROR_CHECK(Gpio_set(pump, BAR_LEVEL_HIGH));
    CpuDelay_ms(500);

    for(int j = 0; j < measure; j++) {
        CpuDelay_ms(550);
    }

    BAR_ERROR_CHECK(Gpio_set(pump, BAR_LEVEL_LOW));
}
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

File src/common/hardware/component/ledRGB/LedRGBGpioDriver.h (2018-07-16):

#ifndef _LED_RGB_GPIO_DRIVER_H_
#define _LED_RGB_GPIO_DRIVER_H_

#include "Gpio.h"

typedef enum eLedMode_t {
    IDEL_LED = 0x00,
    GREEN_LED = 0x01,
    RED_LED = 0x02,
    ORANGE_LED = 0x03,
    BLUE_LED = 0x04,
    GREEN_LED_SLOW_BLINKING = 0x05,
    ORANGE_LED_SLOW_BLINKING = 0x06,
    RED_LED_SLOW_BLINKING = 0x07,
    BLUE_LED_SLOW_BLINKING = 0x08,
    GREEN_LED_FAST_BLINKING = 0x09,
    ORANGE_LED_FAST_BLINKING = 0x0a,
    RED_LED_FAST_BLINKING = 0x0b,
    BLUE_LED_FAST_BLINKING = 0x0c,
    MULTI_2_LED_FAST_BLINKING = 0xd,
    MULTI_3_LED_FAST_BLINKING = 0xe,
    DISABLE_LED = 0xff,
} eLedMode_t;


typedef enum eLedColor_t {
    LED_NOT_DEFINED = 0b000,
    LED_GREEN       = 0b001,
    LED_RED         = 0b010,
    LED_BLUE        = 0b100,
    LED_ORANGE      = (LED_GREEN | LED_RED),
    LED_VIOLET      = (LED_BLUE  | LED_RED),
    LED_BLUE_GREEN  = (LED_BLUE  | LED_GREEN)
} eLedColor_t;

typedef struct sLedRgbConfig {
    eGpioNum_t red;
    eGpioNum_t green;
    eGpioNum_t blue;
} sLedRgbGpioConfig_t;


eBarError_t LedRGBGpioDriver_Init(const sLedRgbGpioConfig_t *config);

eLedColor_t LedRGBGpioDriver_SetColor(const eLedColor_t color);

eLedColor_t LedRGBGpioDriver_ToggleColor(const eLedColor_t color);

eLedColor_t LedRGBGpioDriver_GetColor(void);

#endif /* _LED_RGB_GPIO_DRIVER_H_ */

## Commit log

2018-01-31 project: initial commit.
    [BOM-BAR.xls, customPart.csv]
2018-02-03 schema: add DIY_Machines 3D files
    [Dispensor_Paddle_V2.STL, Idler.STL, Rod_Clamp_V5.STL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]
2018-02-03 motor: update MOTOR_LIMIT define value.
2018-02-03 motor: update time.
2018-02-15 motor: use pomp 3.
2018-02-17 motor: multi pump management.
2018-02-18 cocktail: set initial position for pumps.
2018-02-18 web button: add clean system.
2018-02-18 motor: stop motor if limit switch on X detected.
